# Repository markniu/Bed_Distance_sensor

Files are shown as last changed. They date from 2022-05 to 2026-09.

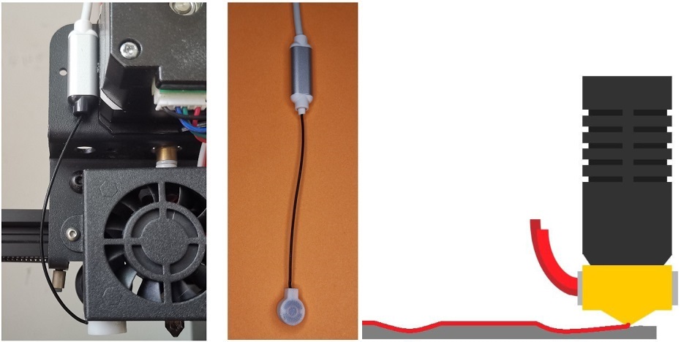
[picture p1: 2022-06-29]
doc/516115054.jpg

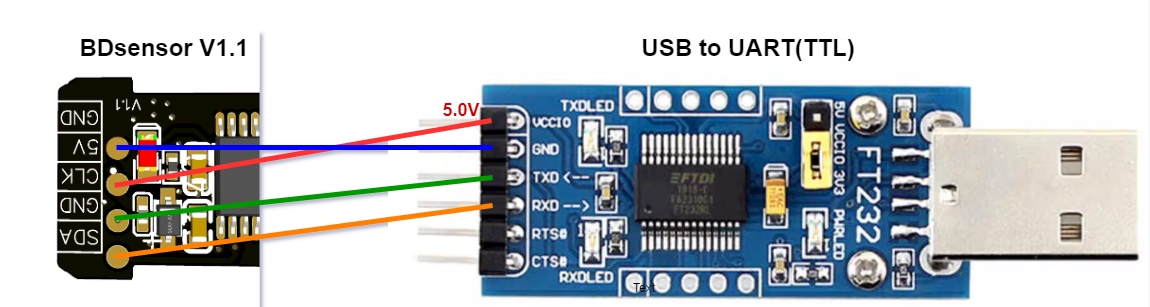
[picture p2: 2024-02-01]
doc/images/flashC51.jpg

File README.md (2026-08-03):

##  The Future of 3D printer Bed Leveling

[BDsensor](https://www.pandapi3d.com/bdsensor) is the first eddy bed level sensor that can work with 3D printer since 2022 and do fast bed leveling and adjust z axis in real time.
it can measure the bed distance at any point in real time without moving the z axis up and down.

Faster leveling, realtime compensation, high accuracy.

### Hardware:
* Shielded Coil
* Work with any GPIO pins(softI2C)
* The lightest and samllest eddy probe, 1.5g:
* Support high temperature chamber(120C) with the long cable probe [BDsensorM](https://github.com/markniu/Bed_Distance_sensor/wiki/BDsensor-M).
### Hardware Version
 . | hardware | firmware/software
--- | --- |---  
2022.6 | BDsensor VA, V1.0 | V1.0  
2023.4 | BDsensor VB, V1.1, the connector was changed | V1.1, support self reboot
2023.11 | BDsensor VB, V1.3, Upgrade the MCU to STM32 | V1.2, for stm32
2024.2  |              |V1.2c, [Support nozzle collision sensing](https://github.com/markniu/Bed_Distance_sensor/wiki/Collision-sensing)
2024.3  | BDsensorM V1.0             | V1.2c
2024.7  | BDsensorM V1.1             |  V1.2c, [Pins order](https://github.com/markniu/Bed_Distance_sensor/issues/178#issuecomment-2319621934) are changed in EXP1 connector
2025.1  |             | [Auto calibration](https://www.pandapi3d.com/post/new-feature-for-bdsensor)

### Software
 . | Marlin | Klipper
--- | --- |---  
Real Time leveling |:heavy_check_mark:| :heavy_check_mark:  
Fast bed mesh |:heavy_check_mark:| :heavy_check_mark: 
Fast bed mesh(No toolhead stop)|:heavy_check_mark: | :heavy_check_mark: 
Distance display |:heavy_check_mark: | :heavy_check_mark: 
Can bus toolhead|No | :heavy_check_mark: 
standby mode automatic while printing|:heavy_check_mark: | :heavy_check_mark: 
[KAMP](https://github.com/kyleisah/Klipper-Adaptive-Meshing-Purging) Adaptive Meshing & Purging |No | :heavy_check_mark: 
nozzle collision sensing|[Detail](https://github.com/markniu/Bed_Distance_sensor/wiki/Collision-sensing-for-Marlin):heavy_check_mark:  | :heavy_check_mark: 

### Benefit of Collision sensing
1.  **Auto z offset calibration**.
2.  **Overcome the temperature drift**.
     The temperature drift will only change the z_offset, it will rise or low the whole bed mesh, but does not change the bed mesh with this BDsensor. that means the bed mesh is the same even with [different temperature](https://www.pandapi3d.com/post/nozzle-collision-sensing-with-bdsensor).
3. Repeatability: **+/-0.005mm**
4. No external hardware and easy to adjust

### What is the difference between VB and VM?
The VB and VM (BDsensorM) share the same electronic design and firmware, so their functions and performance are essentially the same.
* VB: The coil and electronics are installed on the toolhead.
* VM: Only the lightweight 1.5 g coil is installed on the toolhead, while the PCB is mounted away from it, making the VM more suitable for high-temperature chambers up to [120C](https://github.com/markniu/Bed_Distance_sensor/wiki/BDsensor-M).

### Document  : [WiKi](https://github.com/markniu/Bed_Distance_sensor/wiki)

[History](https://hackaday.io/project/185096-0006mm-distance-resolution-sensor-for-3d-printer)

#### Mount STL:  [BLtouch_Compatible](https://www.thingiverse.com/thing:6098131) | [VzBoT](https://discord.com/channels/829828765512106054/1163237892957671424) | [Stealthburner Voron](https://www.printables.com/model/831679-lazy-bd-sensor-adapter-for-stealthburner-voron)

| Channel | Link |
|---|---|
| Discord | [discord.gg/z6ahddnGVU](https://discord.gg/z6ahddnGVU) |
| Facebook group | [facebook.com/groups/380795976169477](https://facebook.com/groups/380795976169477) |
| Where to buy | 🇺🇸 [fabreeko.com](https://fabreeko.com) <br>  🌏 [pandapi3d.com](https://pandapi3d.com) <br> 🇨🇳 [淘宝](https://shop62248922.taobao.com/)  <br> 🇩🇰 [3do.dk](https://3do.dk/12-abl-probe) |

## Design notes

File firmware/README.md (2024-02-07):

How to download the firmware into bdsensor:

[V1.3 STM32](https://github.com/markniu/Bed_Distance_sensor/wiki/Flash-BDsensor(stm32)-firmware)

[V1.1_STC](https://github.com/markniu/Bed_Distance_sensor/wiki/Flash-BDsensor(V1.1)-firmware)

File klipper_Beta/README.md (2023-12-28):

### This is the Beta version patch code for klipper.

if you like to test with this new code please run
```
cd  ~/Bed_Distance_sensor/klipper_Beta/
./install_BDsensor.sh
```
instead of 
```
cd  ~/Bed_Distance_sensor/klipper/
./install_BDsensor.sh
```

in the installation step of Klipper

https://github.com/markniu/Bed_Distance_sensor/wiki/Installing-for-Klipper

#### update: 
#### Add real time leveling. 
November 21, 2023

How to run?   

1. update the files in ~/Bed_Distance_sensor/klipper_Beta
2. go into the folder `cd ~/Bed_Distance_sensor/klipper_Beta`  and run` ./install_BDsensor.sh`
3. compile and flash the klipper.bin firmware again

4. Edit the start gcode in your slicer:
remove the auto bed leveling command `BED_MESH_CALIBRATE` and add `BDSENSOR_SET REAL_TIME_HEIGHT=`xx under the G28,
also z_tilt or gantry level is recommended. 
xx is the max z axis height that will do real time leveling automatically, here we just let this value the same as the first layer height in slicer setting.for example 0.3mm
```
G28
QUAD_GANTRY_LEVEL
G28
BDSENSOR_SET REAL_TIME_HEIGHT=0.3
```

note: this real time leveling works only with the BDsensor and Z motors are connected in the same MCU. 

And install the sensor coil as close to the nozzle as possible.

if you find the nozzle is too close or too far away the bed while printing, please do the calibration again.

#### update:
November 15, 2023

1, add new command:
```
BDSENSOR_VERSION                   //equals M102 S-1
BDSENSOR_CALIBRATE                //equals M102 S-6 
BDSENSOR_READ_CALIBRATION         //equals M102 S-5 
BDSENSOR_DISTANCE                 //equals M102 S-2 
BDSENSOR_SET                           // set value, now only for setting z_adjust, for example BDSENSOR_SET z_adjust=0.1

```
2, invert z_adjust direction as z_offset

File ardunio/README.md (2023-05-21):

Arduino testing code

This is a simple arduino testing code. It read the distance data from BDsensor after initial the communication port.

If you want to do more code by yourself for other application here is the protocol of data 

https://github.com/markniu/Bed_Distance_sensor/wiki/Data-Protocol

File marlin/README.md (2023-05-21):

Install marlin

https://github.com/markniu/Bed_Distance_sensor/wiki/Installing-Bed-Distance-Sensor

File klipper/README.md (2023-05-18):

Installing for Klipper

https://github.com/markniu/Bed_Distance_sensor/wiki/Installing-for-Klipper

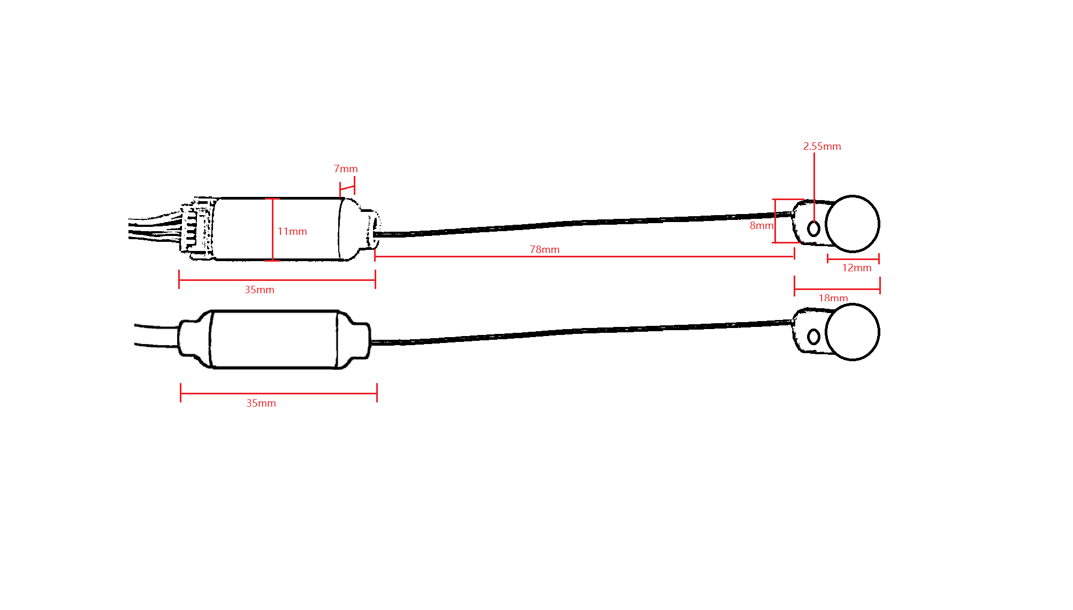
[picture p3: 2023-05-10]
hardware/size.png

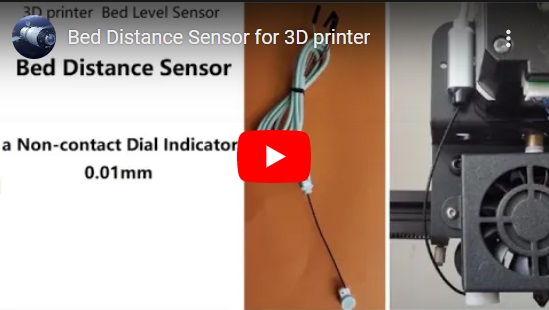
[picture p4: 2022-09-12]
doc/images/mainv.jpg

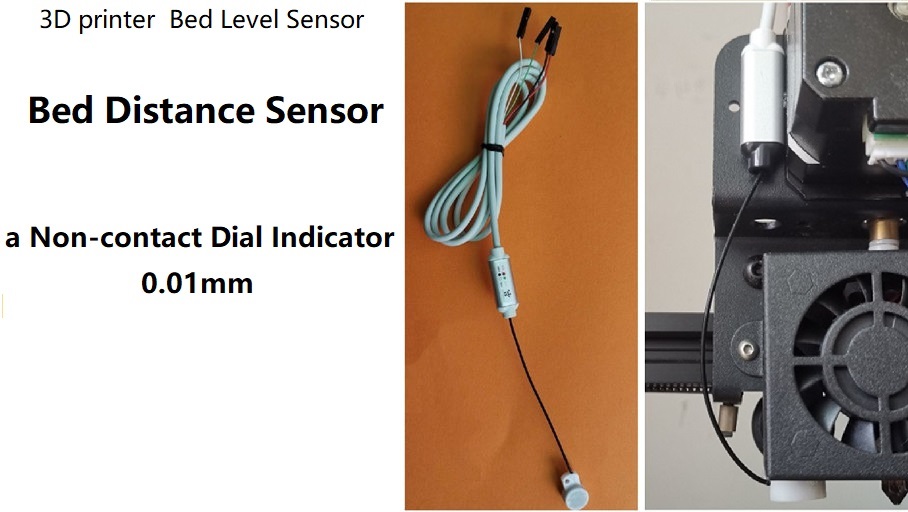
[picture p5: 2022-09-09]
doc/images/mainp2.jpg

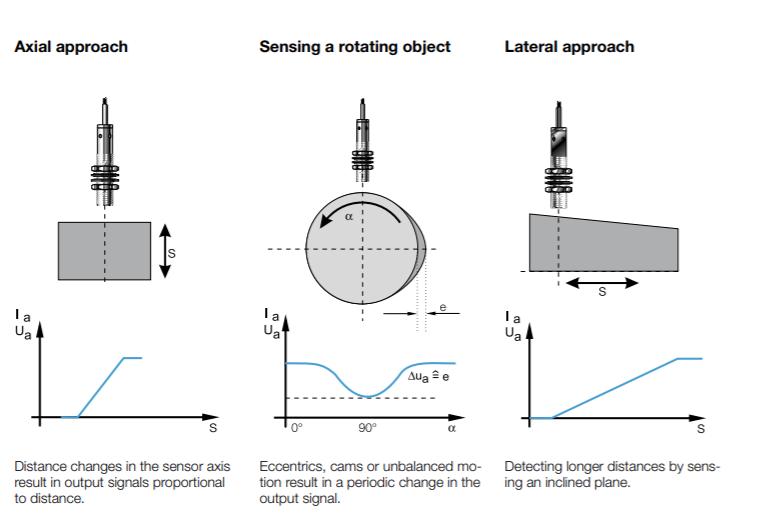
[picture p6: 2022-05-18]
doc/images/Shawn_1.png

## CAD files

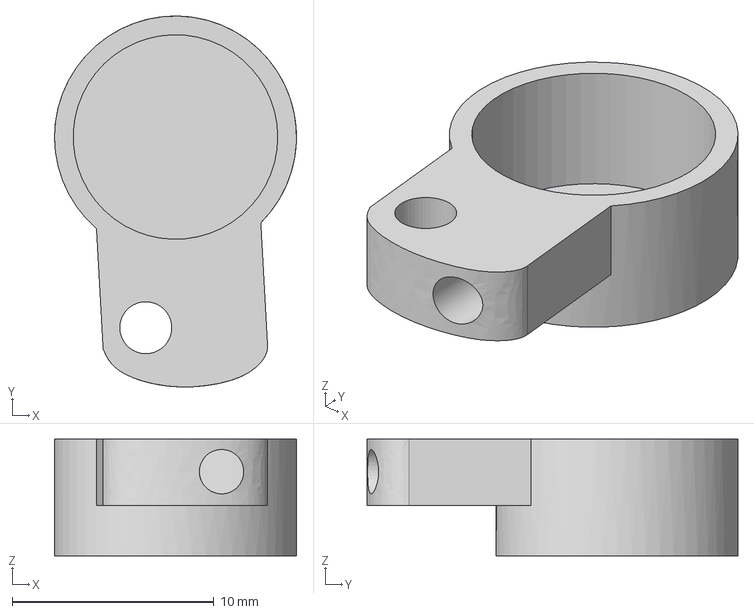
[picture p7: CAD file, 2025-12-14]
hardware/coil_case2025.step
12.0 x 18.4 x 5.80 mm

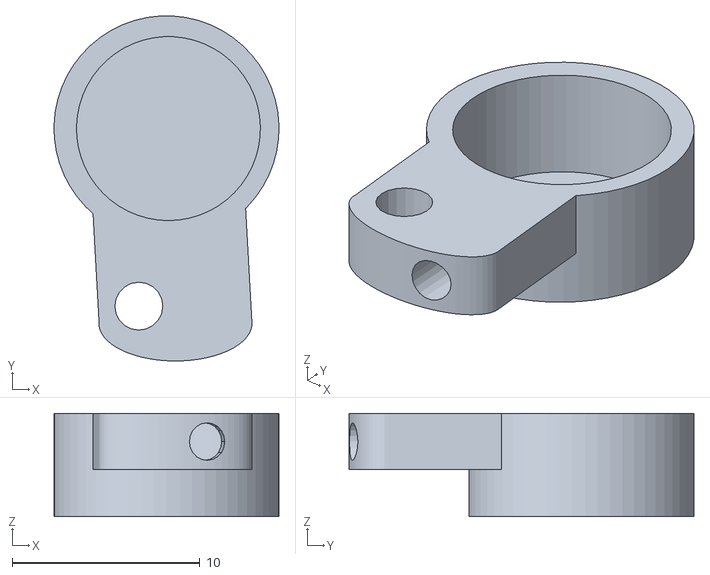
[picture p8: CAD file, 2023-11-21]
stl_size/coil_case_withoutcoil.stl
12.0 x 18.4 x 5.50

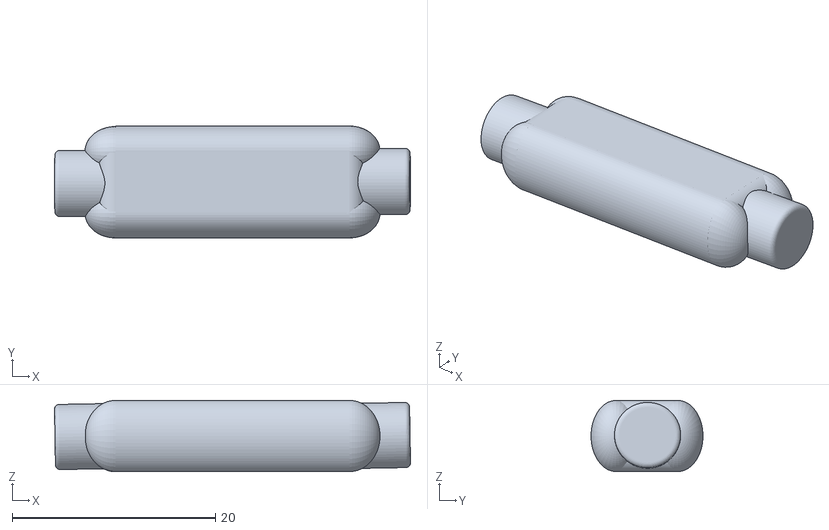
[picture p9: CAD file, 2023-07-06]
hardware/PCB_case.stl
35.0 x 11.0 x 7.00

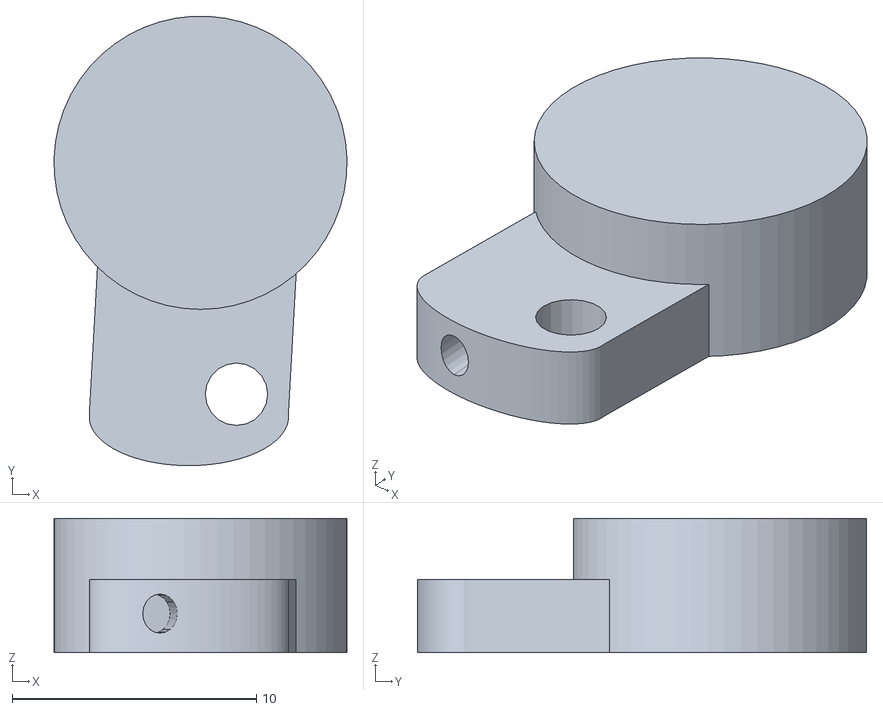
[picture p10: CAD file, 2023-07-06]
stl_size/Coil_casel.stl
12.0 x 18.4 x 5.50

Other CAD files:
hardware/coil_case2025.stl

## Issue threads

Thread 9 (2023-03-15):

Klipper reports: SHUTDOWN  Internal error on command:"M102"

neshami, 2023-03-15:

neshami, 2023-03-15:
Opened by error.
Sorry.

Closed 2023-03-15.

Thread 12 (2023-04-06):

Unable to calibrate sensor on SKR 2B

kendrickxy, 2023-04-06:
Hi,

I have an Anycubic Predator with SKR2B on Marlin.
I am using your branch of [Marlin](https://github.com/markniu/Marlin_for_pull), downloaded yesterday.

I followed the installation steps, but I'm not able to get it to calibrate.

At first, I tried swapping SDA and SCL, but without success.

I've made a few modifications in bdl.cpp from line 175:

```
if (config_state == -6) {
        //BD_I2C_SENSOR.BD_i2c_write(1019); // begin calibrate
        //delay(1000);
        SERIAL_ECHOLNPGM("ENABLE STEPPERS PREcalibrate");
        gcode.stepper_inactive_time = SEC_TO_MS(60 * 5);
        gcode.process_subcommands_now(F("M17 Z"));
        gcode.process_subcommands_now(F("G1 Z-0.05"));
        safe_delay(1000);
        SERIAL_ECHOLNPGM("SET POSITION PREcalibrate");
        gcode.process_subcommands_now(F("G92 Z0"));
        gcode.process_subcommands_now(F("G1 Z0.05"));
        gcode.process_subcommands_now(F("G92 Z0"));
        safe_delay(1000);
        SERIAL_ECHOLNPGM("WHILE START PREcalibrate")

        while (planner.get_axis_position_mm(Z_AXIS) > 0.15) {    // changed >0.00001 to >0.015 and >0.15
  
          safe_delay(10);   // changed (1) to (10)
        }
        SERIAL_ECHOLNPGM("WHILE END PREcalibrate");

        z_pose = 0.00001;
        safe_delay(100);
        BD_I2C_SENSOR.BD_i2c_write(CMD_START_CALIBRATE); // Begin calibrate
        SERIAL_ECHOLNPGM("Begin calibrate");
        safe_delay(200);
        config_state = -7;
      }
```

Below are the outputs for M102 S-1, S-5 and S-6.

```
// M102 S-1

ok
BDsensor version:???????????????????

// M102 S-5

ok
Calibrate data:0,1023, check:0
Calibrate data:1,1023, check:0
Calibrate data:2,1023, check:0
Calibrate data:3,1023, check:0
Calibrate data:4,1023, check:0
Calibrate data:5,1023, check:0
Calibrate data:6,1023, check:0
Calibrate data:7,1023, check:0
Calibrate data:8,1023, check:0
Calibrate data:9,1023, check:0
Calibrate data:10,1023, check:0
Calibrate data:11,1023, check:0
Calibrate data:12,1023, check:0
Calibrate data:13,1023, check:0
Calibrate data:14,1023, check:0
Calibrate data:15,1023, check:0
Calibrate data:16,1023, check:0
Calibrate data:17,1023, check:0
Calibrate data:18,1023, check:0
Calibrate data:19,1023, check:0
Calibrate data:20,1023, check:0
Calibrate data:21,1023, check:0
Calibrate data:22,1023, check:0
Calibrate data:23,1023, check:0
Calibrate data:24,1023, check:0
Calibrate data:25,1023, check:0
Calibrate data:26,1023, check:0
Calibrate data:27,1023, check:0
Calibrate data:28,1023, check:0
Calibrate data:29,1023, check:0
Calibrate data:30,1023, check:0
Calibrate data:31,1023, check:0
Calibrate data:32,1023, check:0
Calibrate data:33,1023, check:0
Calibrate data:34,1023, check:0
Calibrate data:35,1023, check:0
Calibrate data:36,1023, check:0
Calibrate data:37,1023, check:0
Calibrate data:38,1023, check:0
Calibrate data:39,1023, check:0

// M102 S-6

ok
ENABLE STEPPERS PREcalibrate
SET POSITION PREcalibrate
X:0.00 Y:0.00 Z:0.00 E:0.00 Count A:64374B:64374C:64374
X:0.00 Y:0.00 Z:0.00 E:0.00 Count A:64366B:64366C:64366
WHILE START PREcalibrate //stuck in an infinite loop
```

From what we can see in the log above, it's stuck in an infinite loop once reaching `while (planner.get_axis_position_mm(Z_AXIS)>0.00001)`

I've changed `>0.00001` to `>0.015`, but nothing changed.

Any tips on solving the issue?

Thanks

markniu, 2023-04-07:
seems that there had connect problem:
the `check:0 ` means the data check is wrong, the correct value should be `check:1`,
the message after M102 S-1 should be `BDsensor version:V1.0 pandapi3d.com`

did the z motor move while doing calibration?

markniu, 2023-04-07:
Just find the SKR 2 board use the stm32f4x that has higher processing speed than stm32f1, so you can try to increase the delay value from 20 to 100
`#define  I2C_BD_DELAY  100`

kendrickxy, 2023-04-07:
We're getting somewhere!

```
// M102 S-1

ok
BDsensor version:V1.0 pandapi3d.com

// M102 S-5

ok
Calibrate data:0,313, check:1
Calibrate data:1,327, check:1
Calibrate data:2,355, check:1
Calibrate data:3,406, check:1
Calibrate data:4,436, check:1
Calibrate data:5,451, check:1
Calibrate data:6,493, check:1
Calibrate data:7,493, check:1
Calibrate data:8,493, check:1
Calibrate data:9,566, check:1
Calibrate data:10,609, check:1
Calibrate data:11,632, check:1
Calibrate data:12,654, check:1
Calibrate data:13,663, check:1
Calibrate data:14,689, check:1
Calibrate data:15,711, check:1
Calibrate data:16,720, check:1
Calibrate data:17,743, check:1
Calibrate data:18,753, check:1
Calibrate data:19,764, check:1
Calibrate data:20,785, check:1
Calibrate data:21,794, check:1
Calibrate data:22,803, check:1
Calibrate data:23,820, check:1
Calibrate data:24,829, check:1
Calibrate data:25,838, check:1
Calibrate data:26,846, check:1
Calibrate data:27,854, check:1
Calibrate data:28,860, check:1
Calibrate data:29,867, check:1
Calibrate data:30,874, check:1
Calibrate data:31,880, check:1
Calibrate data:32,881, check:1
Calibrate data:33,887, check:1
Calibrate data:34,893, check:1
Calibrate data:35,897, check:1
Calibrate data:36,902, check:1
Calibrate data:37,907, check:1
Calibrate data:38,911, check:1
Calibrate data:39,911, check:1

// M102 S-6

ok
X:0.00 Y:0.00 Z:0.00 E:0.00 Count A:64375B:64375C:64375
X:0.00 Y:0.00 Z:0.00 E:0.00 Count A:64372B:64372C:64372
WHILE BEGIN
```

But as you see it's still stuck in the loop.

I home all 3 axis, send the command `M102 S-6` and the print head lower to the center of the plate as usual.
Once it's there, it's not able to come out of the loop though.

I'll try to run more tests.

markniu, 2023-04-08:
Hi, I think I know what's the problem is the home axis is not allowed before calibration. for the BDsensor is also used as the end stop of Z axis.

kendrickxy, 2023-04-09:
Hi,

At first, I tried to not home before (just tried again now), but it just runs the print head into the bed. not sure why.

Here are the logs I collected (with homing):

```
// M102 S-1

ok
BDsensor version:V1.0 pandapi3d.com

// M102 S-5

ok
Calibrate data:0,313, check:1
Calibrate data:1,327, check:1
Calibrate data:2,355, check:1
Calibrate data:3,406, check:1
Calibrate data:4,436, check:1
Calibrate data:5,451, check:1
Calibrate data:6,493, check:1
Calibrate data:7,493, check:1
Calibrate data:8,493, check:1
Calibrate data:9,566, check:1
Calibrate data:10,609, check:1
Calibrate data:11,632, check:1
Calibrate data:12,654, check:1
Calibrate data:13,663, check:1
Calibrate data:14,689, check:1
Calibrate data:15,711, check:1
Calibrate data:16,720, check:1
Calibrate data:17,743, check:1
Calibrate data:18,753, check:1
Calibrate data:19,764, check:1
Calibrate data:20,785, check:1
Calibrate data:21,794, check:1
Calibrate data:22,803, check:1
Calibrate data:23,820, check:1
Calibrate data:24,829, check:1
Calibrate data:25,838, check:1
Calibrate data:26,846, check:1
Calibrate data:27,854, check:1
Calibrate data:28,860, check:1
Calibrate data:29,867, check:1
Calibrate data:30,874, check:1
Calibrate data:31,880, check:1
Calibrate data:32,881, check:1
Calibrate data:33,887, check:1
Calibrate data:34,893, check:1
Calibrate data:35,897, check:1
Calibrate data:36,902, check:1
Calibrate data:37,907, check:1
Calibrate data:38,911, check:1
Calibrate data:39,911, check:1

// M102 S-6

ok
X:0.00 Y:0.00 Z:0.00 E:0.00 Count A:64354B:64354C:64354
X:0.00 Y:0.00 Z:0.00 E:0.00 Count A:64351B:64351C:64351
WHILE BEGIN
760.437
741.838
723.237
704.638
686.025
667.425
648.825
630.225
611.625
593.025
574.425
555.825
537.225
518.625
500.013
481.413
462.812
444.212
425.613
407.013
388.413
376.975
376.975
376.975
376.975
376.975
376.975
```
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
markniu, 2023-04-10:
Hi, could you share your config files and pins?  actually, I have not tested on the delta printer, the config for the endstop should be different as other printers.   and one other thing you should know is the homing process use the virtual Z_MIN_PIN
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

kendrickxy, 2023-04-10:
Hi,

Most of the issue is solved now :)
Here's the output:

```
// M102 S-1

ok
BDsensor version:V1.0 pandapi3d.com

// M102 S-5

ok
Calibrate data:0,44, check:1 Calibrate data:1,45, check:1
Calibrate data:2,47, check:1 Calibrate data:3,57, check:1
Calibrate data:4,57, check:1 Calibrate data:5,76, check:1
Calibrate data:6,95, check:1 Calibrate data:7,115, check:1
Calibrate data:8,139, check:1 Calibrate data:9,157, check:1
Calibrate data:10,185, check:1 Calibrate data:11,208, check:1
Calibrate data:12,224, check:1 Calibrate data:13,249, check:1
Calibrate data:14,273, check:1 Calibrate data:15,296, check:1
Calibrate data:16,325, check:1 Calibrate data:17,342, check:1
Calibrate data:18,367, check:1 Calibrate data:19,390, check:1
Calibrate data:20,411, check:1 Calibrate data:21,433, check:1
Calibrate data:22,456, check:1 Calibrate data:23,475, check:1
Calibrate data:24,494, check:1 Calibrate data:25,519, check:1
Calibrate data:26,535, check:1 Calibrate data:27,553, check:1
Calibrate data:28,570, check:1 Calibrate data:29,588, check:1
Calibrate data:30,605, check:1 Calibrate data:31,620, check:1
Calibrate data:32,637, check:1 Calibrate data:33,654, check:1
Calibrate data:34,672, check:1 Calibrate data:35,685, check:1
Calibrate data:36,695, check:1 Calibrate data:37,709, check:1
Calibrate data:38,723, check:1 Calibrate data:39,735, check:1

// M102 S-6

ok
X:0.00 Y:0.00 Z:0.00 E:0.00 Count A:30150B:30150C:30150
X:0.00 Y:0.00 Z:0.00 E:0.00 Count A:30150B:30150C:30150
WHILE START
WHILE END!
Begin calibrate
G1 Z0.0 ,Z:0.00 w:0,Zpose:0.00
G1 Z0.1 ,Z:0.10 w:1,Zpose:0.10
G1 Z0.2 ,Z:0.20 w:2,Zpose:0.20
G1 Z0.3 ,Z:0.30 w:3,Zpose:0.30
G1 Z0.4 ,Z:0.40 w:4,Zpose:0.40
G1 Z0.5 ,Z:0.50 w:5,Zpose:0.50
G1 Z0.6 ,Z:0.60 w:6,Zpose:0.60
G1 Z0.7 ,Z:0.70 w:7,Zpose:0.70
G1 Z0.8 ,Z:0.80 w:8,Zpose:0.80
G1 Z0.9 ,Z:0.90 w:9,Zpose:0.90
G1 Z1.0 ,Z:1.00 w:10,Zpose:1.00
G1 Z1.1 ,Z:1.10 w:11,Zpose:1.10
G1 Z1.2 ,Z:1.20 w:12,Zpose:1.20
G1 Z1.3 ,Z:1.30 w:13,Zpose:1.30
G1 Z1.4 ,Z:1.40 w:14,Zpose:1.40
G1 Z1.5 ,Z:1.50 w:15,Zpose:1.50
G1 Z1.6 ,Z:1.60 w:16,Zpose:1.60
G1 Z1.7 ,Z:1.70 w:17,Zpose:1.70
G1 Z1.8 ,Z:1.80 w:18,Zpose:1.80
G1 Z1.9 ,Z:1.90 w:19,Zpose:1.90
G1 Z2.0 ,Z:2.00 w:20,Zpose:2.00
G1 Z2.1 ,Z:2.10 w:21,Zpose:2.10
G1 Z2.2 ,Z:2.20 w:22,Zpose:2.20
G1 Z2.3 ,Z:2.30 w:23,Zpose:2.30
G1 Z2.4 ,Z:2.40 w:24,Zpose:2.40
G1 Z2.5 ,Z:2.50 w:25,Zpose:2.50
G1 Z2.6 ,Z:2.60 w:26,Zpose:2.60
G1 Z2.7 ,Z:2.70 w:27,Zpose:2.70
G1 Z2.8 ,Z:2.80 w:28,Zpose:2.80
G1 Z2.9 ,Z:2.90 w:29,Zpose:2.90
G1 Z3.0 ,Z:3.00 w:30,Zpose:3.00
G1 Z3.1 ,Z:3.10 w:31,Zpose:3.10
G1 Z3.2 ,Z:3.20 w:32,Zpose:3.20
G1 Z3.3 ,Z:3.30 w:33,Zpose:3.30
G1 Z3.4 ,Z:3.40 w:34,Zpose:3.40
G1 Z3.5 ,Z:3.50 w:35,Zpose:3.50
G1 Z3.6 ,Z:3.60 w:36,Zpose:3.60
G1 Z3.7 ,Z:3.70 w:37,Zpose:3.70
G1 Z3.8 ,Z:3.80 w:38,Zpose:3.80
G1 Z3.9 ,Z:3.90 w:39,Zpose:3.90
End calibrate data
```

The problem came from bdl.cpp as suspected. I simply replaced all `planner.get_axis_position_mm(Z_AXIS)` with `current_position.z`. Not sure why the command was off.

Still, I'm having some issues leveling the bed using automatic leveling `#define AUTO_BED_LEVELING_UBL`.

Here's my Z_MIN_PIN configuration:

```
#define Z_MIN_PIN          			         I2C_BD_SDA_PIN
#define Z_MIN_PROBE_PIN                  I2C_BD_SDA_PIN  //for skr2B
```

The command M119 outputs TRIGGERED when the nose is touching the bed. Though, not as the light turns on. I'm assuming it's working as expected.

Attached you can find my config files and pins.
[Configuration_adv.h.txt](https://github.com/markniu/Bed_Distance_sensor/files/11192941/Configuration_adv.h.txt)
[Configuration.h.txt](https://github.com/markniu/Bed_Distance_sensor/files/11192943/Configuration.h.txt)
[pins_BTT_SKR_V2_0_common.h.txt](https://github.com/markniu/Bed_Distance_sensor/files/11192946/pins_BTT_SKR_V2_0_common.h.txt)

markniu, 2023-04-24:
this issue of calibration is the same as https://github.com/markniu/Bed_Distance_sensor/issues/13#issuecomment-1517310271  , I have pulled it to marlin github, I think the next version of marlin will be updated.

Closed 2023-04-25.

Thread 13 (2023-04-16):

check:0

gacek4000, 2023-04-16:
Hi, I have SKR 1.4 and Marlin-2.1.2. After connecting the BD sensor I keep getting "Calibrate data:28,1023, check:0". The red LED lights up when something metal is under the sensor, then the "BD sensor Z" value on the display changes from 10.14 to 0.0
Any ideas ?

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

i set:

#define  I2C_BD_SDA_PIN    P0_01  // Please change to the actual number which the SDA wire is connected to your mainboard
#define  I2C_BD_SCL_PIN    P0_00  // Please change to the actual number which the SCL wire is connected to your mainboard
#define  I2C_BD_DELAY  20

//#define Z_MIN_PROBE_USES_Z_MIN_ENDSTOP_PIN
// Force the use of the probe for Z-axis homing
//#define USE_PROBE_FOR_Z_HOMING

#define BD_SENSOR
#define Z_SAFE_HOMING
and so on...

markniu, 2023-04-17:
you can replace those 2 files with the following link:
https://github.com/markniu/Marlin_for_pull/blob/bugfix-2.1.x/Marlin/src/feature/bedlevel/bdl/bdl.cpp
https://github.com/markniu/Marlin_for_pull/blob/bugfix-2.1.x/Marlin/src/gcode/probe/M102.cpp

then you can send M102 S-1 to read the version of BDsensor that can help you to check if the connection is success.

gacek4000, 2023-04-17:
before replacing the 2 files you described:
https://photos.app.goo.gl/fSZpwm4N7xALxyRs5

after change:
https://photos.app.goo.gl/6uFVhADqvVGMHKbYA
additionally, in this case, instead of "BD sensor Z: 10.14" on the screen, there is "Settings stored" from the beginning

i2c configuration didn't change anything in either case

markniu, 2023-04-18:
That should be all the old calibrate data in the BDsensor has been erased to default 0xFF,  Please sending M102 S-6 and waiting it finished.

gacek4000, 2023-04-18:
<facepalm>
ill check after job, thanks man !

gacek4000, 2023-04-18:
No, it doesn't work. It behaves the same as at the beginning: it starts moving down at the default speed. When I start the calibration, I have a screwdriver under the sensor, the LED was on red.

markniu, 2023-04-18:
the z axis should moving up.
and please make sure the calibration is finished by waiting there is message "End calibrate data" return back. or else there will return back 1023 and check 0 after M102 S-5

gacek4000, 2023-04-18:
when i send M102 S-6 the head goes down quite fast, nothing shows up in the console. homing and other head control from pronterface works fine

gacek4000, 2023-04-18:
I just replaced 'current_position.z' like kendrickxy and after 'M102 S-6' the head went down again, but in the console I had:

Begin calibration
G1Z0.0 ,Z:0.00
w:0,Zpose:0.00
G1Z0.1 ,Z:0.10
w:1,Zpose:0.10
G1Z0.2 ,Z:0.20
w:2,Zpose:0.20
G1Z0.3 ,Z:0.30
w:3,Zpose:0.30
G1Z0.4 ,Z:0.40
w:4,Zpose:0.40
G1Z0.5 ,Z:0.50

when I set
#define Z_MIN_PIN I2C_BD_SDA_PIN
#define Z_MIN_PROBE_PIN I2C_BD_SDA_PIN

printer behavior as above

[Configuration_adv.txt](https://github.com/markniu/Bed_Distance_sensor/files/11263324/Configuration_adv.txt)
[Configuration.txt](https://github.com/markniu/Bed_Distance_sensor/files/11263325/Configuration.txt)
[pins_BTT_SKR_common.txt](https://github.com/markniu/Bed_Distance_sensor/files/11263326/pins_BTT_SKR_common.txt)
[pins_BTT_SKR_V1_4.txt](https://github.com/markniu/Bed_Distance_sensor/files/11263327/pins_BTT_SKR_V1_4.txt)
[bdl.txt](https://github.com/markniu/Bed_Distance_sensor/files/11263328/bdl.txt)

gacek4000, 2023-04-18:
* M119 pokazuje 'z_probe: open' bez względu co jest pod czujnikiem (dioda świeci/ nie świeci)
* Z_MIN_PROBE_ENDSTOP_INVERTING true/false odpowiednio zmienia 'z_probe: open/triggered' ale głowa w obu przypadkach idzie na dół przy M102 S-6

markniu, 2023-04-19:
please add this `||P == Z_MIN_PROBE_PIN` in the endstop.cpp  like
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

and try M119 again

markniu, 2023-04-19:
> * M119 shows 'z_probe: open' no matter what is under the sensor (LED on/off)
> * Z_MIN_PROBE_ENDSTOP_INVERTING true/false changes 'z_probe: open/triggered' accordingly but the head goes down on M102 S-6 in both cases

The homing position of your delta printer is the in the max position, but the calibration position is in the zero, so the head will go down to the zero after the calibration command M102 S-6.  recommend to checking the position before calibration by send gcode M114

gacek4000, 2023-04-19:
i did what you said and:

M119
Reporting endstop status
x_max: open
y_max: open
z_max: open
z_probe: open
filament: open
ok

with metal under sensor. calibration process - still the same.

'#define Z_MIN_PROBE_PIN                  P0_10'    is this correct ? When I uncomment it, the program doesn't compile

markniu, 2023-04-20:
although I haven't delta printer but have one SKRV1.4 board, I will run it on that board late or tomorrow late. and will update that after testing.

markniu, 2023-04-21:
[bdl.zip](https://github.com/markniu/Bed_Distance_sensor/files/11292705/bdl.zip)
I have test it with skrV1.4 board, and it can do calibration and M119 success.  please replace the those files. including the file probe.h in Marlin\src\module folder. and don't homing printer before calibration.

gacek4000, 2023-04-23:
It works ! everything works, screen and calibration. Thanks a lot buddy :) What have you done? Have I mixed something up?

markniu, 2023-04-24:
That's great, thanks for test it on delta printer.
the position value got by  `planner.get_axis_position_mm(Z_AXIS)` is not zero in zero position for delta printer, so I fixed it by  `planner.get_axis_position_mm(Z_AXIS)-pos_zero_offset`

gacek4000, 2023-04-25:
Hi again, I guess I rushed to announce success :( calibration works, M119 also but:
when trying to calibrate the delta (G33) or when trying to print a test print, the head goes down and does not react to the presence of the table under the sensor and collides with the table.
i set "#define DELTA_HEIGHT" and #define "Z_MAX_POS" to be less than the height of the printer. Then, when going down, even though I put metal under the sensor (the LED is on), the printer does not respond and then goes back up and I get a "Homing Failed" error
Any ideas ?

Closed 2023-04-24.

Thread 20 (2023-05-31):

Question: What is the operating temperature/ melting point?

billgeek, 2023-05-31:
As most that have built a Voron extruder will know, inductive probes tend to melt due to the constant exposure of the probe to the heated bed, especially when printing using ABS where the bed sits at around 85C.

What temperature resistance does this sensor have and will it deform or melt while in operation?

markniu, 2023-06-02:
the max operating temperature of all the components is above 80C including the wires.
the max work temperature of the inside coil is 120C, and 170C for the nylon case.

Closed 2023-06-02.

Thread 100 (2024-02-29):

Endstop triggered during retract when it is not triggered.

nullifyr, 2024-02-29:
Mark, I added another z axis motor to my SKR2 and put the gantry on ball screws to get rid of gantry sag that I could not tune away.
Calibration works great. Testing the measurement after calibration, the Z axis is very accurate now.
But now I can't get the Z to home. No matter where I place the gantry, well above the bed or very near it, I get a "Endstop z still triggered after retract" even if the M119 shows the endstop is open when I start homing.
Nothing changed on the printer other than the addition of a 2209 stepper driver
I attached the log with the relevant dump
[sklippy.log](https://github.com/markniu/Bed_Distance_sensor/files/14441199/sklippy.log)
[printerlog.txt](https://github.com/markniu/Bed_Distance_sensor/files/14441200/printerlog.txt)
You can see in the printer log where I calibrate, measure, move the gantry down above the trigger point, measure and check triggers then repeat that after moving the gantry below the trigger point.
I also have re-cloned the bdsensor repo, made a clean firmware and flashed it.
This is the newest version of your sensor with the long sensor lead that you sent along with my last order. It definitely worked before this change. I believe there is some bug I introduced.

nullifyr, 2024-02-29:
I turned on collision homing and it works now?
```
G28
BDsensorVer:V1.2c pandapi3d ,switch_mode=1,collision_homing=1
pos:0.80 new:0.87 auto adjust Z axis +0.07mm,Raw data from 748.0 to 755.0
```

markniu, 2024-02-29:
seems it was triggered in the place where the nozzle did not touch on the bed.
maybe the homing speed and second homing speed of z motor is too slow.

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

nullifyr, 2024-02-29:
I raised the homing to 8 and second homing to 0.8, but the nozzle is still ~3mm away from the bed when at Z0

markniu, 2024-02-29:
What's the configuration of the BDsensor , stepper_z  safe_z_home? and they are not in the log file.

> Mark, I added another z axis motor to my SKR2 and put the gantry on ball screws to get rid of gantry sag that I could not tune away. Calibration works great. Testing the measurement after calibration, the Z axis is very accurate now. But now I can't get the Z to home. No matter where I place the gantry, well above the bed or very near it, I get a "Endstop z still triggered after retract" even if the M119 shows the endstop is open when I start homing. Nothing changed on the printer other than the addition of a 2209 stepper driver I attached the log with the relevant dump [sklippy.log](https://github.com/markniu/Bed_Distance_sensor/files/14441199/sklippy.log) [printerlog.txt](https://github.com/markniu/Bed_Distance_sensor/files/14441200/printerlog.txt) You can see in the printer log where I calibrate, measure, move the gantry down above the trigger point, measure and check triggers then repeat that after moving the gantry below the trigger point. I also have re-cloned the bdsensor repo, made a clean firmware and flashed it. This is the newest version of your sensor with the long sensor lead that you sent along with my last order. It definitely worked before this change. I believe there is some bug I introduced.

markniu, 2024-02-29:
try to increase the second homing speed to 3
> I raised the homing to 8 and second homing to 0.8, but the nozzle is still ~3mm away from the bed when at Z0

nullifyr, 2024-02-29:
Second homing at 1.6 seems to have done the trick
[klippy.log](https://github.com/markniu/Bed_Distance_sensor/files/14441629/klippy.log)
Here is the full Klipper log.
If I turn off collision homing I am back to the retract error.

nullifyr, 2024-02-29:
Here is the log after I change back to no
[klippy.log](https://github.com/markniu/Bed_Distance_sensor/files/14441670/klippy.log)

markniu, 2024-02-29:
how about take the bdsensor off the hotend also the whole wires for bdsensor to avoid the noise from other wires , and put the sensor coil close or away from the bed while homing to see if it works as expected.

nullifyr, 2024-02-29:
OK I tried all your suggestions, it did not change the retract message with collision homing off.
The behavior never changes, close to the bed or far away.
I even put the coil on a 100mm standoff so it was far away from the toolhead. No change there.
I tried the older version of the sensor too. It does the same thing.

nullifyr, 2024-03-02:
Is there any way to get bdsensor to report the state of the endstops before it performs any movement?
I cannot figure out how to fix my problem here.

Collision homing does work, but it occasionally reads > 0.3mm of adjustment
is there any way to set a maximum adjustment the collision homing will allow before it fails?
for instance, if there is a glob of plastic on the nozzle and we do collision homing, the adjustment is wild
`pos:0.80 new:1.62 auto adjust Z axis +0.82mm,Raw data from 81.0 to 124.0`
Needless to say this print failed instantly because the nozzle was several layers higher than it should have started at.

markniu, 2024-03-02:
I also tryed your configure and did not met this problem, could you take a video about that homing process?
> OK I tried all your suggestions, it did not change the retract message with collision homing off. The behavior never changes, close to the bed or far away. I even put the coil on a 100mm standoff so it was far away from the toolhead. No change there. I tried the older version of the sensor too. It does the same thing.

nullifyr, 2024-03-02:
[https://youtu.be/gmcaOjzPdys](https://youtu.be/gmcaOjzPdys)

The gantry never tries to drop down. The Z is immediately triggered. But, you see me move over the trigger range (the move was 10mm) and I did M119, it was open before I pressed home.

Other things I have done
Corrected the Z motor phase and direction so both motors have the same configuration.
Trammed the bed again just to be sure

markniu, 2024-03-02:
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

you can replace the BDsensor.py with this new one that I add a debug info into the code,
[BDsensor.zip](https://github.com/markniu/Bed_Distance_sensor/files/14468116/BDsensor.zip)

nullifyr, 2024-03-02:
[klippy (12).log](https://github.com/markniu/Bed_Distance_sensor/files/14468290/klippy.12.log)`

Klipper state: Shutdown

triggered at 10.150 mm !

Endstop z still triggered after retract

home_start:0.800000

home_start:0.800000

BDsensorVer:V1.2c pandapi3d ,switch_mode=1,collision_homing=0

G28`

nullifyr, 2024-03-02:
I tried some more things but still no joy
-Removed TMC Autotuning and KAMP
-Tried different pins for SDA/SCL
-Went back to the old version of the sensor with a short lead for the coil

With the old version I can see the LED while the homing is in process. It never lights up like it does when it is actually triggered.
I am so confused by that.

nullifyr, 2024-03-04:
YES.
That fixed it.

```
11:04 AM
Z axis triggered at 0.040 mm,auto adjusted by BDsensor.
11:04 AM
home_start:0.100000
11:04 AM
home_start:0.100000
11:04 AM
BDsensorVer:V1.2c pandapi3d ,switch_mode=1,collision_homing=0
```

nullifyr, 2024-03-04:
Could you clarify what the problem actually was?

markniu, 2024-03-12:
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

Hello, just want to know if it is totally fixed the problem in your printer, and that never happened again? did you try other value of this position_endstop ?

nullifyr, 2024-03-12:
Totally fixed the problem.
Unless I raise the position_endstop to 0.8mm or more. Then the behavior comes back. This is fine for me as the coil is 0.625mm away from the nozzle tip, but I think it would be a problem for anyone who wanted to mount higher than 0.8mm.

markniu, 2024-03-13:
Thanks, that's also confused me for that I have not repeated this problem in myside. I will debug more. but now I think it could be the communication problem by the signal noise on the cable.

here the position_endstop is not the mount height. it just the trigger position that we set to avoid the nozzle crash into bed with higher homing speed.

markniu, 2024-03-22:
> Totally fixed the problem. Unless I raise the position_endstop to 0.8mm or more. Then the behavior comes back. This is fine for me as the coil is 0.625mm away from the nozzle tip, but I think it would be a problem for anyone who wanted to mount higher than 0.8mm.

someone feedbacked me that the latest update of BD_sensor.c had fixed this issue with  position_endstop : 0.8mm, maybe you can try it if you have time and feedback here too. thanks!

nullifyr, 2024-03-23:
```
Klipper state: Shutdown
triggered at 10.150 mm
Endstop z still triggered after retract
home_pos:80
home_pos:80
BDsensorVer:V1.2c pandapi3d ,switch_mode=1,collision_homing=0,collision_cal=0
G28
Klipper state: Disconnect
FIRMWARE_RESTART
Z triggered at 0.700 mm,auto adjusted.
home_pos:70
home_pos:70
BDsensorVer:V1.2c pandapi3d ,switch_mode=1,collision_homing=0,collision_cal=0
G28
```
No change in behavior. I agree it seems like noise, but when the configuration has position_endstop at 0.7mm the sensor works very well. Well enough that I can level the gantry to 0.008mm in 3 tries. Wouldn't noise affect the readings for probes like that?

Could you make a version that raises the Z to some set distance over the trigger height before it tries to home? I know Klipper already has this logic in the homing code, but I can't think of any other way to test this.

Closed 2024-03-04.

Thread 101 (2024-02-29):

Issue with ramps 1.4

luco85, 2024-02-29:
Hi, i tried to install to my printer with ramps 1.4, but klipper crash and shutdown whenr i send any commansd whit M102. I have a bltouch working and no issue when installed bd patch. There is any chance to use with this board or need to use the gpio pin of rpi? In this case can i use any gpio for SDA and CLK?

markniu, 2024-02-29:
you can use the gpio of rpi, #92

luco85, 2024-02-29:
Ok i'll try. Another issue that i had was after add the moonraker update section. After that i had  an UNKNOW state to update section of mainsail. Any info?

luco85, 2024-03-01:
> you can use the gpio of rpi, #92

It work fine with rpi. For UNKNOW label in update manager do you have any tip?

luco85, 2024-03-04:
I wanted to ask you to do the integration with klipper! good News!
I installed bd sensor to rpa and work fine! very nice device. thank you!

luco85, 2024-03-06:
@markniu hi! Yesterday i tried to use the collision feature. I update bdsensor section with homing and calibration collision set to 1. When i read sensor it respond firmware v1.2, switch mode 0, collision homing 1, collision calibrate 1. When i run calibration it work as before, it not homing but start to calibrate. I updated your code to last and flashed all mcu. I noticed when i run your code to update i have an error. So need to uninstall and reinstall to update

markniu, 2024-03-06:
The respond firmware should be `V1.2c` not `V1.2 ` , else maybe the firmware did not flash successfully.

luco85, 2024-03-06:
I suspected this so yesterday I ordered st link to flash device

luco85, 2024-03-09:
@markniu hi, there is a typo error here
Marco for display distance on Screen
not Marco but Macro ;)

markniu, 2024-03-10:
> @markniu hi, there is a typo error here Marco for display distance on Screen not Marco but Macro ;)

Thank you :)

markniu, 2024-03-28:
the latest BD_sensor.c code on github has fixed the issue on ramps1.4 board.

Closed 2024-03-28.

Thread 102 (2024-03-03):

Can't home with new firmware

Mharasim1, 2024-03-03:
After flashing new firmware im getting this error when trying to home z: Unable to read tmc uart 'stepper_z' register DRV_STATUS
Z axis moves fine if i use SET_KINEMATIC_POSITION
There are a few BD Sensor errors in klippy.log
[klippy (9).log](https://github.com/markniu/Bed_Distance_sensor/files/14473712/klippy.9.log)

markniu, 2024-03-04:
did it happen every time while homing? how about send M102 S-1 before homing gcode G28?

Mharasim1, 2024-03-04:
I get this after sending M102 S-1 : BDsensorVer:V1.1bpandapi3d.com ,switch_mode=1,collision_homing=1,collision_cal=1
but it still doesent home.
It was homing before i flashed new firmware to the sensor
@markniu

markniu, 2024-03-04:
the bd sensor and tmc are two independed from the hardware and code.
one way you can try to debug:  remove the BDsensor section and replace the `endstop_pin: probe:z_virtual_endstop` with `endstop_pin:PB8` in the stepper_z section, move the nozzle far enough from the bed and home again

markniu, 2024-03-04:
for the klippery source code, seems the error is that it can not read data from the tmc and timeout.
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

Mharasim1, 2024-03-05:
I removed bd sensor section and and removed endstop_pin: probe:z_virtual_endstop and it tried to home fine.
but when i add bd sensor to config i get tmc error

markniu, 2024-03-07:
could you try to replace a code in the BDsensor.py as following? that will let the homing process as old firmware.

before
```
  def home_start(self, print_time, sample_time, sample_count, rest_time,
                   triggered=True):
        self.BD_Sensor_Read(2)
        if "V1." not in self.bdversion:
            self.BD_version(self.gcode)
        clock = self.mcu_endstop.print_time_to_clock(print_time)
```

after

```

  def home_start(self, print_time, sample_time, sample_count, rest_time,
                   triggered=True):
        self.BD_Sensor_Read(2)
        self.switch_mode = 0
        clock = self.mcu_endstop.print_time_to_clock(print_time)

```

Closed 2024-04-15.

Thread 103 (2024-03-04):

Internal error on command:"G28" while homing Z axis

BUGBEAR7, 2024-03-04:
Hello ,

Recently installed on my Enderwire , after calibration Z axis is not homing gets Internal error on command:"G28"
Here is the [klippy.log](https://github.com/markniu/Bed_Distance_sensor/files/14481264/klippy.log)
I am not sure what I am doing wrong , Sensor is v1.2

markniu, 2024-03-04:
the reason is the aliases board pins, please use the PB8 PB9 instead of PROBE_2 PROBE_1

BUGBEAR7, 2024-03-04:
Thanks for that , it fixed the issue.

Closed 2024-03-04.

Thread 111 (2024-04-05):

No data or corrupt data from BDsensor( )

hidara2000, 2024-04-05:
Hi,
I have two of these devices and am getting the same error on both

## WIRING
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

## EBB sb2209 from guide
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

Servos = PB9
Probe = PB8

## Klipper Settings
```
[BDsensor]
# Don't use aliases for the board pins
sda_pin: EBBCan: PB9 # from https://github.com/markniu/Bed_Distance_sensor/issues/50
scl_pin: EBBCan: PB8
delay: 20 # 20us per pulse, this value should be >=18 but must be below 30
z_offset:0 #  within -0.6 to 0.6mm
x_offset: 0
y_offset: 25.0
no_stop_probe: # fast probe that the toolhead will not stop at the probe point,disable it by commenting out.
position_endstop: 0.5 #the Z axis will be triggered after it measured the distance is below this value(mm) while homing z, recommend value is 0.5~1.0
#speed:0.8 # this speed only works for the z tilt and PROBE_ACCURACY command.
collision_homing:0 #  set it 1 to enable homing with nozzle collision sensing.
collision_calibrate:0 # set it 1 to enable auto calibrate BDsensor with nozzle collision sensing.
```

## Flashing using canbus result
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

## BDsensor.py exists before compiling and flashing clean
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

## WHAT I'VE TRIED
- swap   PB8 for  PB9 in klipper settings
- check wires for shorts and continuity - all good

## Results from commands
```
M119
```
x:open y:open z:TRIGGERED # whether triggered or not
*NOTE: I can see the light triggering to detect metal when I bring a spanner close to the sensor*

```
M102 S-1
```
No data or corrupt data from BDsensor( ), Please check connection

```
BDSENSOR_VERSION
```
No data or corrupt data from BDsensor( ), Please check connection

```
BDSENSOR_READ_CALIBRATION
```
No data or corrupt data from BDsensor( ), Please check connection
BDSensor mounted too close! please mountthe BDsensor 0.2~0.4mm higher

hidara2000, 2024-04-05:
Also tried direct connection to MKS v1.3 board and same issue. Bl touch with confi changes works perfectly using the same pins

markniu, 2024-04-05:
Hello,
Seems you need to switch the SDA and CLK pin in the printer.cfg:
```
sda_pin: EBBCan: PB8
scl_pin: EBBCan: PB9
```

hidara2000, 2024-04-05:
Cheers for the reply. That's what I had originally but changed it as per the comment in this post https://github.com/markniu/Bed_Distance_sensor/issues/50

either way I've tried both

markniu, 2024-04-05:
you can change it back to the correct order and try again.
if still the same,  try to connect the bdsensor to the mainboard for finding out where the problem is.

hidara2000, 2024-04-05:
I've already tried that and connected directly to the SKR v1.3

markniu, 2024-04-05:
the endstop pin on the skr v1.3 for the bltouch doesn't work with bdsensor, you can use the pin in EXP1 or EXP2 for bdsensor.

> SKR v1.3

hidara2000, 2024-04-05:
I have the EBB SB2209 canbus and need to get it working with this. If it needs I2C I found (image below) in the schematics but cant figure out which pins these are.

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

markniu, 2024-04-05:
BDsensor use the i2c, but not standard i2c.
I have tested the other version of EBB board that can work with bdsensor with the BLtouch port.
do you check the wires with multimeter?

> Also just a quick one. The pins for the BDsensor mention sda and clk. Does it use I2c? if so, I wonder if the pins for BLTouch on the EBB SB2209 are compatible?

hidara2000, 2024-04-05:
do you check the wires with multimeter?

I checked for continuity and shorts

markniu, 2024-04-05:
ok, because I have met the connection loosen problem to the mainboard before.
are there any other unused pins on the board?you can try that, but don't use the endstop pins.

markniu, 2024-04-05:
also did the led work? the led on the bdsensor should be light on if it detects the metal.

hidara2000, 2024-04-05:
LED works as expected

markniu, 2024-04-05:
you can also try to increase the delay value in the [BDsensor] section from 20 to 40, that will slow down the data transfer speed.

Terrradives, 2024-04-06:
I also have been having the same symptoms and issues the last few days.  I'm plugged into a octopus 1.1.  pb6 &7 pins.  lights work.  triggered always active.  M102 codes return the same.

hidara2000, 2024-04-10:
Hi @Terrradives ,
Did you manage to get it working?

hidara2000, 2024-04-10:
@markniu

Any suggestions on how to connect directly to a Pi and if there is a Python script I can run to test the device?

markniu, 2024-04-10:
yes, you can test it with the gpio on the Pi,  connect the bdsensor to the gpio on the PI like gpio17 and gpio27.

[BDsensor]
....
scl_pin = host:gpio17
sda_pin = host:gpio27

compile and flash firmware:
https://www.klipper3d.org/RPi_microcontroller.html

https://github.com/markniu/Bed_Distance_sensor/issues/84

hidara2000, 2024-04-10:
Donno if this will help but I added the following lines to the BDsensor.py
``` python
attrs = vars(self)
attrs = ('\n'.join("%s: %s" % item for item in attrs.items()))

self.gcode.respond_info(f"{attrs}")
self.gcode.respond_info("No data or corrupt data from BDsensor(%s), "
                                    "Please check connection"%self.bdversion)
```
and the response was
```
printer: <__main__.Printer object at 0x7f7f9350d0>
config:
name: BDsensor
z_adjust: 0.0
z_offset: 0.0
position_endstop: 0.5
stow_on_each_sample: True
no_stop_probe:
collision_homing: 0
collision_calibrate: 0
activate_gcode:
deactivate_gcode:
collision_calibrating: 0
switch_mode: 1
bdversion:             
next_cmd_time: 0.0
action_end_time: 0.0
sda_pin_num: PB8
mcu:
_invert: 0
oid: 2
mcu_endstop:
_invert_endstop: 0
oid_endstop: 2
endstop_pin_num: PB8
endstop_bdsensor_offset: 0
cmd_queue:
trapq:
trapq_append:
trapq_finalize_moves:
stepper_kinematics:
bd_sensor:
gcode:
I2C_BD_receive_cmd2: None
gcode_move:
bedmesh: None
bd_value: 10.24
results: []
finish_home_complete: None
wait_trigger_complete: None
multi: OFF
adjust_range: 0
old_count: 1000
homeing: 0
reactor:
status_dis: None
_rest_ticks: 0
_trdispatch:
_trsyncs: [, ]
ncont: 0
z_last: 0
I2C_BD_receive_cmd:
_home_cmd:
toolhead:
```

markniu, 2024-04-10:
> Donno if this will help but I added the following lines to the BDsensor.py
>
that reported all the data is 10.24(`bd_value: 10.24`) , means no data returned from the sda pin.

hidara2000, 2024-04-10:
Interesing....
When I connected the device to the EBB canbus or directly to the SKR v1.3 I got errors

Now when connected directly to the pi I get
```
BDSENSOR_VERSION
```
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

markniu, 2024-04-10:
yes, that's weird.

markniu, 2024-04-10:
you can try to test it by connecting it to the pins on the EXP1 of SKR

Terrradives, 2024-04-10:
I have not yet.  I’m kind of hoping there are tests I can rule things out with.  I’ve switched pins I was using on the octopus board, so I don’t think it’s board or pins.  I’ve got a bltouch currently working on those pins.  It’s not wire.  So I’m left kind of thinking how do I verify I’ve got a correctly flashed boards or verify the sensor is fully functional.Sent from my iPhoneOn Apr 10, 2024, at 12:26 AM, hidara2000 ***@***.***> wrote:
Hi @Terrradives ,
Did you manage to get it working?

—Reply to this email directly, view it on GitHub, or unsubscribe.You are receiving this because you were mentioned.Message ID: ***@***.***>

hidara2000, 2024-04-13:
**GOT IT WORKING :)**

## What didn't work
1. Made 3 sets of cables from the supplied ribbon.
Used the proper crimping tool.
Checked for shorts and continuity.
None of these cables worked on the BDsensor but all worked for a BL-touch I had lying around
2. Reflashed firmware on EBB and SKR

## What DID work
1. Made a set of cables using some 26AWG silicone cables. 1st set worked on both BL touch and BDsensor

hidara2000, 2024-04-13:
PS for anyone else, here's a mount I made for the CW2 & Stealthburner. You don't need to modify any existing parts.

https://www.printables.com/model/831679-lazy-bd-sensor-adapter-for-stealthburner-voron

markniu, 2024-04-13:
> PS for anyone else, here's a mount I made for the CW2 & Stealthburner. You don't need to modify any existing parts.
>
> https://www.printables.com/model/831679-lazy-bd-sensor-adapter-for-stealthburner-voron

Thanks for share!

Terrradives, 2024-04-13:
Is there any chance you’d be willing to make a1.5 meter set and ship them to the USA?Sent from my iPhoneOn Apr 13, 2024, at 12:59 AM, hidara2000 ***@***.***> wrote:
GOT IT WORKING :)
What didn't work

Made 3 sets of cables from the supplied ribbon.
Used the proper crimping tool.
Checked for shorts and continuity.
None of these cables worked on the BDsensor but all worked for a BL-touch I had lying around
Reflashed firmware on EBB and SKR

What DID work

Made a set of cables using some 26AWG silicone cables. 1st set worked on both BL touch and BDsensor

—Reply to this email directly, view it on GitHub, or unsubscribe.You are receiving this because you were mentioned.Message ID: ***@***.***>

hidara2000, 2024-04-14:
@Terrradives
Honestly I would diy this. Just grab the following
- https://www.amazon.com/dp/B08RMQP6YP?ref=ppx_yo2ov_dt_b_product_details&th=1
- https://www.amazon.com/Electrical-26-Flexible-Silicone-different/dp/B07G2LRX68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

For each of the 5 wires, cut off the male ends of two pre-crimped wires and solder the length you need in between. The set comes with heat shrink as well :)

Closed 2024-04-14.

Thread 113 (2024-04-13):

re:Beta, after running 'install_BDsensor.sh', firmware compilation fails with Error 255

m3hrz4d, 2024-04-13:
I cloned the repo, then successfully ran 'klipper_Beta/install_BDsensor.sh', but when trying to compile firmware, it fails just before the end with Error 255" Any ideas that could point me in the right direction?
```
make
Using default symbol values (no '/home/sonic/klipper/.config')
Configuration saved to '/home/sonic/klipper/.config'
  Creating symbolic link out/board
Loaded configuration '/home/sonic/klipper/.config'
Configuration saved to '/home/sonic/klipper/.config'
  Creating symbolic link out/board
  Creating symbolic link out/board
  Building out/autoconf.h
  Compiling out/src/sched.o
  Compiling out/src/command.o
  Compiling out/src/basecmd.o
  Compiling out/src/debugcmds.o
  Compiling out/src/initial_pins.o
  Compiling out/src/gpiocmds.o
  Compiling out/src/stepper.o
  Compiling out/src/endstop.o
  Compiling out/src/trsync.o
  Compiling out/src/adccmds.o
  Compiling out/src/spicmds.o
  Compiling out/src/sdiocmds.o
  Compiling out/src/i2ccmds.o
  Compiling out/src/pwmcmds.o
  Compiling out/src/buttons.o
  Compiling out/src/tmcuart.o
  Compiling out/src/neopixel.o
  Compiling out/src/pulse_counter.o
  Compiling out/src/lcd_st7920.o
  Compiling out/src/lcd_hd44780.o
  Compiling out/src/spi_software.o
  Compiling out/src/i2c_software.o
  Compiling out/src/thermocouple.o
  Compiling out/src/sensor_adxl345.o
  Compiling out/src/sensor_angle.o
  Compiling out/src/sensor_mpu9250.o
  Compiling out/src/sensor_lis2dw.o
  Compiling out/src/sensor_ldc1612.o
  Compiling out/src/sensor_bulk.o
  Compiling out/src/BD_sensor.o
  Compiling out/src/stm32/watchdog.o
  Compiling out/src/stm32/gpio.o
  Compiling out/src/stm32/clockline.o
  Compiling out/src/stm32/dfu_reboot.o
  Compiling out/src/generic/crc16_ccitt.o
  Compiling out/src/generic/armcm_boot.o
  Compiling out/src/generic/armcm_irq.o
  Compiling out/src/generic/armcm_reset.o
  Compiling out/src/../lib/stm32f4/system_stm32f4xx.o
  Compiling out/src/stm32/stm32f4.o
  Compiling out/src/generic/armcm_timer.o
  Compiling out/src/stm32/gpioperiph.o
  Compiling out/src/stm32/adc.o
  Compiling out/src/stm32/i2c.o
  Compiling out/src/stm32/spi.o
  Compiling out/src/stm32/sdio.o
  Compiling out/src/stm32/serial.o
  Compiling out/src/generic/serial_irq.o
  Compiling out/src/stm32/hard_pwm.o
  Building out/compile_time_request.o
Too many message ids
make: *** [Makefile:84: out/compile_time_request.o] Error 255
```

markniu, 2024-04-13:
hello, you can try this https://github.com/markniu/Bed_Distance_sensor/issues/47#issuecomment-1825045187

m3hrz4d, 2024-04-14:
that fixed the issue! thank you!

Closed 2024-04-14.

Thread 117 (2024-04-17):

No data or corrupt data from BDsensor(                    ), Please check connection

Townie-au, 2024-04-17:
My setup was broken. So i had to reinstall everything.
I am having an issue with katapult not being able to access after flashing the ebb42.
So I have to flash klipper via stm32 programmer.
I connected bdsensor to the ebb42 when flashing klipper after installing bdsensor.
Now I get this error all the time.
Im using BD Sensor v1.
Everything was working including the bd sensor yesterday.
[klippy (27).log](https://github.com/markniu/Bed_Distance_sensor/files/15009506/klippy.27.log)
[printer.txt](https://github.com/markniu/Bed_Distance_sensor/files/15009519/printer.txt)

Ive checked continuity on the lead from the sensor to the board. OK
Canboard communicating via CAN0.
I just tried rolling back klipper to the previous version but no change.

Got katapult and klipper working still no chnage for bd sensor.

Townie-au, 2024-04-17:
Ive checked continuity on the lead from the sensor to the board. OK
Canboard communicating via CAN0.

Townie-au, 2024-04-18:
Is the bd sensor dead? Please help

markniu, 2024-04-18:
you can test BDsensor with the gpio on the Pi.

connect the bdsensor to the gpio on the PI like gpio17 and gpio27.

[mcu host]
serial: /tmp/klipper_host_mcu

[BDsensor]
....
scl_pin: host:gpio17
sda_pin: host:gpio27

compile and flash firmware:
https://www.klipper3d.org/RPi_microcontroller.html

https://github.com/markniu/Bed_Distance_sensor/issues/111#issuecomment-2046685001

Townie-au, 2024-04-18:
Ok.
Got it working somewhat by flashing the beta firmware.
M102 s-1 returns nothing
M102 s-6 calibrates successfully
However when I go to home z I get "Bed Distance Sensor data error:10.24"
When I first started klipper up I got "collision_homing in printer.cfg invalid". So I commented out both collison homing lines.

markniu, 2024-04-18:
Glad to hear it works again.

Townie-au, 2024-04-18:
What about this Mark?
However when I go to home z I get "Bed Distance Sensor data error:10.24"

markniu, 2024-04-18:
if M102 s-1 returns nothing or 10.24 means the same connection problem.

markniu, 2024-04-18:
did you modify the cable before or just the software?

Townie-au, 2024-04-18:
> did you modify the cable before or just the software?

Just the software.

markniu, 2024-04-18:
for finding out what's the problem hardware or software, I think you can try the gpio on the pi.

Townie-au, 2024-04-18:
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

host: Current version v0.12.0-124-g09a78c31
Up-to-date MCU(s):
<none>

Once the underlying issue is corrected, use the "RESTART"
command to reload the config and restart the host software.

mcu 'host': Unknown command: I2C_BD_send

Townie-au, 2024-04-18:
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

I connected the BD Sensor to my main board, recompiled and reflashed both EBB and M5P and got the same result. :(

markniu, 2024-04-18:
how about use the gpio in the EXP1? E.g. PB6 PB7

Townie-au, 2024-04-18:
> how about use the gpio in the EXP1? E.g. PB6 PB7

Im going to try the RPI.

Townie-au, 2024-04-18:
3.2 40 Pins GPIO
When Manta series motherboard work with CB1, 40 pins GPIO is a custom IO arrangement, as shown in the figure below, Pin 7 is CB1's "PC7", and Pin 11 is CB1's "PC14". The GPIO number of CB1 corresponds to (Px–PA)*32 + Pin
For example:
PC7 = (PC–PA)*32 + 7 = 2 * 32 + 7 = 71
PH10 = (PH–PA)*32 + 10 = 7 * 32 + 10 = 234
PC7 is numbered in Klipper as pin: host: gpio71, PH10 as pin: host: gpio234

WTH. Trying to make sense of this. I am using pin 6 and pin 8.

Townie-au, 2024-04-18:
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

Townie-au, 2024-04-18:
OMG. Finally worked it out. GPIO78 and GPIO74
Same error on CB1 GPIO.

markniu, 2024-04-18:
> OMG. Finally worked it out. GPIO78 and GPIO74 Same error on CB1 GPIO.

worked on RPI GPIO?

Townie-au, 2024-04-18:
> > OMG. Finally worked it out. GPIO78 and GPIO74 Same error on CB1 GPIO.
>
> worked on RPI GPIO?

No. Same error. No data or corrupt data from BDsensor(                    ), Please check connection

markniu, 2024-04-18:
what's the hardware version of bdsensor?

Townie-au, 2024-04-18:
> what's the hardware version of bdsensor?

How do I tell?

markniu, 2024-04-18:
there is a version text on the sensor on the other side of the white connector, like v1.3 or v1.1

Townie-au, 2024-04-18:
v1.1

markniu, 2024-04-18:
does the led on the sensor work? it will light on if it detects the metal else off.

Townie-au, 2024-04-18:
> does the led on the sensor work? it will light on if it detects the metal else off.

Yes led lights up when metal is brought nearby

markniu, 2024-04-18:
then from the hardware, we can only to find if the problem is from the dead mcu or the cable.
do you have one more cable to replace the old one for the bdsensor?

Townie-au, 2024-04-18:
> then from the hardware, we can only to find if the problem is from the dead mcu or the cable. do you have one more cable to replace the old one for the bdsensor?

No I dont. I checked the cable with the multimeter.

markniu, 2024-04-18:
if you have a solder tool you can try to connect to a serial model, there will be many useful data output from the serial com port.

Townie-au, 2024-04-18:
Do I need to open the case for that?

markniu, 2024-04-18:
> Do I need to open the case for that?

No
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

Townie-au, 2024-04-18:
Would a ST LINK work?

markniu, 2024-04-18:
> Would a ST LINK work?

No, the MCU on the v1.1 is not stm32

Townie-au, 2024-04-18:
> > Would a ST LINK work?
>
> No, the MCU on the v1.1 is not stm32

Would you be able to send me another bd sensor please?
Ill get the USB>UART converter and debug this one for you.

markniu, 2024-04-18:
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

No problem, send me an email with your shipping address.

Townie-au, 2024-04-18:
Thankyou 👍👍👍
What's your email?

markniu, 2024-04-18:
niujl123@sina.com

Townie-au, 2024-04-20:
I've sent you the email mark and I've ordered the adapter. Should get here Tuesday.
What commands do I send to retrieve the data?

markniu, 2024-04-20:
> I've sent you the email mark and I've ordered the adapter. Should get here Tuesday. What commands do I send to retrieve the data?

any serial software is ok, like pronterface.  no command needed.

Townie-au, 2024-04-20:
> > I've sent you the email mark and I've ordered the adapter. Should get here Tuesday. What commands do I send to retrieve the data?
>
> any serial software is ok, like pronterface. no command needed.

Does it need to be plugged into the printer as well or just read it straight from the sensor?

What do I need to look for?

markniu, 2024-04-20:
no need to be plugged into the printer.  there will be some message output after it is powered on, and many raw data output. then we can confirm whether this sensor works well.

Townie-au, 2024-04-25:
64▒$4▒▒▒▒▒▒▒▒▒▒▒▒▒▒▒▒▒▒yy▒4e▒▒▒G▒5▒▒▒55▒䊊▒F▒▒!!1▒▒F▒!▒▒▒▒)▒▒))▒▒▒▒▒N▒▒▒▒▒D▒5ڃ▒%!▒▒▒!▒͂▒▒!▒▒1▒▒1▒▒▒▒5▒1▒!!!▒▒▒▒▒▒▒▒▒▒▒)▒▒▒▒▒▒9▒▒9▒▒▒9▒5▒▒Ń▒▒)▒i▒▒)))9▒▒▒▒▒▒▒▒▒▒)▒▒599▒▒▒▒▒9▒)▒▒▒)▒▒%ձ45)▒▒▒▒▒▒5)▒)▒)5▒▒)▒▒▒▒5▒▒▒5)▒%▒ɱ▒▒ʂ▒▒▒)▒▒▒▒▒▒ł)▒▒▒▒▒▒▒▒▒▒)▒)D▒▒▒)))▒▒▒d▒▒▒d▒▒▒▒▒g▒)▒5▒▒)▒▒▒▒䙂▒d▒▒4▒▒▒))▒)▒)5))i▒▒)▒▒)▒▒▒▒▒▒▒▒₂▒▒▒▒䂂)▒)▒▒▒▒)▒▒▒▒▒▒▒▒ʶ▒▒▒)▒▒)▒▒▒▒▒▒▒▒▒▒▒▒)5▒▒))▒▒5▒▒ʂ▒▒)D▒▒▒▒▒▒)i▒▒▒▒▒▒▒▒5▒▒▒▒▒▒▒▒̂▒䂾5▒▒▒▒▒▒▒▒▒▒▒▒▒▒)▒

markniu, 2024-04-25:
> 64▒$4▒▒▒▒▒▒▒▒▒▒▒▒▒▒▒▒▒▒yy▒4e▒▒▒G▒5▒▒▒55▒䊊▒F▒▒!!1▒▒F▒!▒▒▒▒)▒▒))▒▒▒▒▒N▒▒▒▒▒D▒5ڃ▒%!▒▒▒!▒͂▒▒!▒▒1▒▒1▒▒▒▒5▒1▒!!!▒▒▒▒▒▒▒▒▒▒▒)▒▒▒▒▒▒9▒▒9▒▒▒9▒5▒▒Ń▒▒)▒i▒▒)))9▒▒▒▒▒▒▒▒▒▒)▒▒599▒▒▒▒▒9▒)▒▒▒)▒▒%ձ45)▒▒▒▒▒▒5)▒)▒)5▒▒)▒▒▒▒5▒▒▒5)▒%▒ɱ▒▒ʂ▒▒▒)▒▒▒▒▒▒ł)▒▒▒▒▒▒▒▒▒▒)▒)D▒▒▒)))▒▒▒d▒▒▒d▒▒▒▒▒g▒)▒5▒▒)▒▒▒▒䙂▒d▒▒4▒▒▒))▒)▒)5))i▒▒)▒▒)▒▒▒▒▒▒▒▒₂▒▒▒▒䂂)▒)▒▒▒▒)▒▒▒▒▒▒▒▒ʶ▒▒▒)▒▒)▒▒▒▒▒▒▒▒▒▒▒▒)5▒▒))▒▒5▒▒ʂ▒▒)D▒▒▒▒▒▒)i▒▒▒▒▒▒▒▒5▒▒▒▒▒▒▒▒̂▒䂾5▒▒▒▒▒▒▒▒▒▒▒▒▒▒)▒

the baud rate should be 115200

markniu, 2024-04-25:
that's the raw data from the mcu, and seems the sensor works well.

Townie-au, 2024-04-25:
> that's the raw data from the mcu, and seems the sensor works well.

So why the error in mainsail mark?

Townie-au, 2024-04-25:
> that's the raw data from the mcu, and seems the sensor works well.

I want it to work again. :(
Where do we go from here?

markniu, 2024-04-27:
I think it only to check the connection/pin number and try to increase the delay value in the BDsensor section.

Townie-au, 2024-05-12:
Hey Mark
Thank you so much for sending the new sensor.
It worked straight away. With the cable I was using before. I didn't use your one because it's too long just to go to the tool head and I didn't want to cut it.
Unless it's an intermittent thing. I'll keep you posted.
How do I use the realtime leveling?

Closed 2024-05-17.

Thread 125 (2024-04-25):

Probe goes nuts

P1t0u, 2024-04-25:
This is my probe: BDsensorVer:V1.1 pandapi3d.com ,switch_mode=0,collision_homing=0,collision_cal=0

It is connected to the BL Touch port on a BTT Manta M5P
[BDsensor]
sda_pin: PC13
scl_pin: PC15
delay: 20
x_offset: -33
y_offset: 0
no_stop_probe:
position_endstop: 0.5
collision_homing:0
collision_calibrate:0

KLIPPER and the bed sensor code were updated on Apr 16, the MCU was reflashed  at that time.  This has been going on since I installed the probe about a month ago.

It will work for a while then it says it is triggered when it is clearly not.

M119
x:open y:open z:open
G28 Z
triggered at 10.150 mm
warning:triggered at 0mm, Please slow down the homing z speed
Z triggered at 0.000 mm,auto adjusted.
M119
x:open y:open z:open

The probe is actually about 120MM from the bed and the LED is OFF

I will then power cycle the printer and all is good for a while; then it will go nuts again

markniu, 2024-04-26:
did you calibrate the bdsensor? and what's the data returned after M102 S-5 ?

P1t0u, 2024-04-26:
Yes I ran M102 S-6, here is the M102 S-5 data:
1015
1015
1015
1015
1015
976
976
976
964
943
921
902
880
857
837
817
794
770
749
727
704
681
661
640
614
589
565
541
517
492
469
444
419
369
369
345
315
287
262

The probe is about 2mm from the tip of the nozzle, I tried making the gap smaller in order to get closer to 100 for the first reading but then I did not have 10 between the first and second values.

G1 Z1
BDSENSOR_DISTANCE
1.02mm

markniu, 2024-04-27:
you can add `homing_retract_dist:0` in the section stepper_z.
and also attach klipply.log

P1t0u, 2024-04-27:
As requested I added homing_retract_dist:0 in my configuration, a few minutes later I changed the filament in the printer and upon loading the new filament I had the error which I confirmed with:
G28 Z
triggered at 10.030 mm
warning:triggered at 0mm, Please slow down the homing z speed
Z triggered at -0.120 mm,auto adjusted.

The probe is 180mm from the bed and M119 correctly reports x:open y:open z:open

I am attaching klippy.log
[klippy-5.log](https://github.com/markniu/Bed_Distance_sensor/files/15139166/klippy-5.log)

markniu, 2024-04-28:
what's the returned value after M102 S-2 instead of M119, it seems the returned value is -0.12

markniu, 2024-04-28:
I also suspect the electrinic noise from other wires for example the motor or heater.
could you try the
G28 Z
G28 Z

P1t0u, 2024-04-28:
G28
triggered at 10.150 mm
warning:triggered at 0mm, Please slow down the homing z speed
Z triggered at 0.000 mm,auto adjusted.
M119
x:open y:open z:open
M102 S-2
BDsensor:Out of measure Range or too close to the bed

Sadly M102 S-2 is useless in this case.

Further testing allowed me to get the error on demand, every time I loaded or unloaded the filament I could not home Z properly.  Right now I am at the point where it seems that the probe cable does not like running in the cable chain alongside the extruder stepper motor cable (I have run many print jobs successfully so I don't think the hot end is involved, the extruder stepper motor gets to spin faster while loading and unloading the filament so that is my number one suspect).  I have installed another cable on the outside of the cable chain and went from 100% failures to 0%.  The sampling is still pretty small so I won't call it solved just yet but it looks much better.

Now I need to figure out a permanent way to affix the probe cable on the outside of the cable chain.

markniu, 2024-04-29:
someone also report this electromagnetic interference recently, so now I just updated the new cable back to the same as first version  bdsensor, that is shielded, twisted pairs and high purity copper wire for preventing EMI. it will be shipped with the bdsensor now instead of the old cables in the stock.
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

P1t0u, 2024-04-29:
That sounds really nice…. Can I have one?

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

markniu, 2024-04-30:
> That sounds really nice…. Can I have one?
yes, please send me your shipping address to my email: niujl123@sina.com

lunatec84, 2024-05-08:
I’ve got the same errors and it’s not the 30mm long cable to the Toolboard of my printer! Meanwhile I’ve ruined 2 Bondtech CHT nozzles, the second 350x350mm not so cheap CR3D PEI flex-plate and wasted about 65€ filament with this sensor! Now this sensor looks like really bad beta crap to me. Three month ago, there are a lot of bugs with CAN toolboard timer to close error messages and false z value readings, I’ve ruined the first PEI flex-plate and switched back to quickdraw probe. Yesterday I gave this sensor another try, flashed the firmware to the v1.3 sensor, and compiled and flashed Klipper on the EBB36 using CAN speed at 1M. Calibrated the probe, scratched the bed with the nozzle while doing a QGL (bug), printed 3 parts with perfect first layers and then, I’m getting the same timer to close error after 6,5 hours and 75% finished print, wasting 640g Fiberlogy PA12CF15. With the collision probing, the first 5 attempts were okay and at the 6. attempt, the nozzle crashed hardly into the printbed and ruined with the force of the 4 Z motors, parts from the quad gantry and toolhead. I’m totally pissed off with this crap buggy sensor. With the quickdraw probe QGL was fine, why the heck is your code when doing a QGL, moving at first z down in the center of the bed and moving in this low height to the QGL corner points and scratching the unleveled bed with the nozzle, instead of moving to a safe z height, moving to the first corner point, measuring, moving z back to save height and doing the 3 remaining gantry level points in the same way? That wasn’t the case with earlier versions. Heaters where off during probing, because it gives me false sensor readings and sensor calibration values where also okay on the four calibration attempts I’ve tried. With the money I’ve wasted meanwhile in destroyed parts from this crap sensor usage,  I’ve could bought 4-5 out of the box working beacon sensors! I don’t think that it is a good idea to include this buggy sensor and code in klipper at this time.

markniu, 2024-05-08:
I am so sorry for that waste and thank you for the support and feedback those helpful information.
the timer too close should be the new bug caused by the recent code committed that I have not test too much.
and about the QGL there is a new quad_gantry_level_probe:1  that can let the probe up and down while doing QGL.

lunatec84, 2024-05-08:
In January 2024, I also encountered issues where the timer to close error appeared with this sensor. Even with your code patched into Klippy, the error occurred intermittently when the sensor wasn't in use. This isn't a new bug, and I'm not the only one experiencing these errors. Today, I've reduced the power, speed, and acceleration for Z-axis movements to prevent further damage caused by sensor or code failures. However, the QGL problem persists despite enabling QGL collision probing. The code needs to be adjusted to include a configurable save Z height variable for movements between QGL points, as a belt-driven gantry can unevenly move 10-20mm when stepper motors get unpowered, potentially causing damage to the printer bed or other components. Additionally, the QGL code seems to ignore given z_hop values. Another issue I encountered today was a Toolboard MCU move queue overflow in mid-print. I suspect that sensor data is overloading the CAN bus even at 1Mbit on a fast printer. Moreover, the sensor occasionally triggers in mid-air, and its LED flickers when it's in the triggered range. It's possible that my sensor is faulty. I’m thinking about opening the sensor housing and connecting the analog pin from the sensor chip to an oscilloscope for further analysis. It would also be helpful if you could provide another sensor for testing. At some points I was near to the trash bin with this sensor or making a video from the actual status and a report, but the only thing beware me from that, is the point that if it worked correctly some times, it’s doing a really good job and i would see this sensor in the official klipper repo soon, but for now there are definitely too much and too heavy bugs for including it. I would give you further informations, feedback and helping you to get this sensor reliable, because I know that it’s not an easy task, especially when real-time comes into play.

markniu, 2024-05-08:
Thank you so much for far more test , please send me your shipping address with email:niujl123@sina.com, I would like to send you the 2 type of new sensor for test.

> In January 2024, I also encountered issues where the timer to close error appeared with this sensor. Even with your code patched into Klippy, the error occurred intermittently when the sensor wasn't in use. This isn't a new bug, and I'm not the only

Closed 2024-06-09.

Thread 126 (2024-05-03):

Klipper calibration issue

dhoard, 2024-05-03:
I had to rebuild my Klipper machine, so I needed to recalibrate the printer/BDsensor.

I ran through the [instructions](https://github.com/markniu/Bed_Distance_sensor/wiki/Installing-for-Klipper ) and found that I had issues at [step 5](https://github.com/markniu/Bed_Distance_sensor/wiki/Installing-for-Klipper#5-calibration).

"Send command SET_KINEMATIC_POSITION Z=50  then move the Z axis down in the menu until the nozzle just touches the bed plate, the BDsensor will use this position as the zero position."

If the toolhead is located further than 50mm above the print plate when issuing the command, then Klipper wouldn't allow enough Z movement to move the nozzle down to "just touch the bed."

```
Move out of range: 0.000 0.000 -.100 [0.000]
```

I worked around the issue by...

1. disabling the steppers in Klipper
2. manually rotating the Z lead screw(s) so that the nozzle "just touches the bed."
3. issuing `SET_KINEMATIC_POSITION Z=0`
4. continue with the remaining calibration instructions

Post-calibration tests seem correct.

Thoughts on changing the instructions?

markniu, 2024-05-04:
seems the 50mm is not enough, you can set it to 200, `SET_KINEMATIC_POSITION Z=200`  I also have updated that in the instruction.

Closed 2024-05-04.

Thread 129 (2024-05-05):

Homing X or Y causes Z to appear as though it was homed

markleaf131313, 2024-05-05:
Whenever I home X or Y independently the Z automatically becomes homed as well, though it never did the homing.

When I turn off the motors (M84) it crashes with the error "MCU 'host' shutdown: Invalid oid type". I am using sensorless homing and have the homing overriden with the gcode below and in the console BDsensor I guess outputs the leveling height.

```
Klipper state: Shutdown
Real time leveling height:0.000000
M84
```

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

```
[gcode_macro _HOME_X]
gcode:
    # Always use consistent run_current on A/B steppers during sensorless homing
    {% set RUN_CURRENT_X = printer.configfile.settings['tmc2209 stepper_x'].run_current|float %}
    {% set RUN_CURRENT_Y = printer.configfile.settings['tmc2209 stepper_y'].run_current|float %}
    {% set HOME_CURRENT = 0.7 %}
    SET_TMC_CURRENT STEPPER=stepper_x CURRENT={HOME_CURRENT}
    SET_TMC_CURRENT STEPPER=stepper_y CURRENT={HOME_CURRENT}
    SAVE_GCODE_STATE NAME=STATE_HOME_X

    # Home
    G28 X
    # Move away
    G91
    G1 X65 F1200

    # Wait just a second… (give StallGuard registers time to clear)
    G4 P500
    # Set current during print
    SET_TMC_CURRENT STEPPER=stepper_x CURRENT={RUN_CURRENT_X}
    SET_TMC_CURRENT STEPPER=stepper_y CURRENT={RUN_CURRENT_Y}
    RESTORE_GCODE_STATE NAME=STATE_HOME_X

[gcode_macro _HOME_Y]
gcode:
    # Set current for sensorless homing
    {% set RUN_CURRENT_X = printer.configfile.settings['tmc2209 stepper_x'].run_current|float %}
    {% set RUN_CURRENT_Y = printer.configfile.settings['tmc2209 stepper_y'].run_current|float %}
    {% set HOME_CURRENT = 0.7 %}
    SET_TMC_CURRENT STEPPER=stepper_x CURRENT={HOME_CURRENT}
    SET_TMC_CURRENT STEPPER=stepper_y CURRENT={HOME_CURRENT}
    SAVE_GCODE_STATE NAME=STATE_HOME_Y

    # Home
    G28 Y
    # Move away
    G91
    G1 Y-75 F1200

    # Wait just a second… (give StallGuard registers time to clear)
    G4 P500
    # Set current during print
    SET_TMC_CURRENT STEPPER=stepper_x CURRENT={RUN_CURRENT_X}
    SET_TMC_CURRENT STEPPER=stepper_y CURRENT={RUN_CURRENT_Y}
    RESTORE_GCODE_STATE NAME=STATE_HOME_Y

[homing_override]
axes: xyz
set_position_z: 0
gcode:
    {% set home_all = 'X' not in params and 'Y' not in params and 'Z' not in params %}
    SAVE_GCODE_STATE NAME=STATE_HOME_OVERRIDE

    {% if home_all or 'X' in params %}
        _HOME_X
    {% endif %}

    {% if home_all or 'Y' in params %}
        _HOME_Y
    {% endif %}

    {% if home_all or 'Z' in params %}
        G28 Z
    {% endif %}

    RESTORE_GCODE_STATE NAME=STATE_HOME_OVERRIDE
```

markleaf131313, 2024-05-06:
My mistake I see where it is setting the Z now.

Closed 2024-05-06.

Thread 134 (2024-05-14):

make command error

ibrahimhakkicandan, 2024-05-14:
when i try to make command with bdsensor installed it gives "Too many message ids
make: *** [Makefile:84: out/compile_time_request.o] Error 255"

Here is the full log:

pi@mainsail:~/klipper $ make
  Creating symbolic link out/board
  Building out/autoconf.h
  Compiling out/src/sched.o
  Compiling out/src/command.o
  Compiling out/src/basecmd.o
  Compiling out/src/debugcmds.o
  Compiling out/src/initial_pins.o
  Compiling out/src/gpiocmds.o
  Compiling out/src/stepper.o
  Compiling out/src/endstop.o
  Compiling out/src/trsync.o
  Compiling out/src/adccmds.o
  Compiling out/src/spicmds.o
  Compiling out/src/sdiocmds.o
  Compiling out/src/i2ccmds.o
  Compiling out/src/pwmcmds.o
  Compiling out/src/buttons.o
  Compiling out/src/tmcuart.o
  Compiling out/src/neopixel.o
  Compiling out/src/pulse_counter.o
  Compiling out/src/lcd_st7920.o
  Compiling out/src/lcd_hd44780.o
  Compiling out/src/spi_software.o
  Compiling out/src/i2c_software.o
  Compiling out/src/thermocouple.o
  Compiling out/src/sensor_adxl345.o
  Compiling out/src/sensor_angle.o
  Compiling out/src/sensor_mpu9250.o
  Compiling out/src/sensor_lis2dw.o
  Compiling out/src/sensor_ldc1612.o
  Compiling out/src/sensor_bulk.o
  Compiling out/src/BD_sensor.o
  Compiling out/src/stm32/watchdog.o
  Compiling out/src/stm32/gpio.o
  Compiling out/src/stm32/clockline.o
  Compiling out/src/stm32/dfu_reboot.o
  Compiling out/src/generic/crc16_ccitt.o
  Compiling out/src/generic/armcm_boot.o
  Compiling out/src/generic/armcm_irq.o
  Compiling out/src/generic/armcm_reset.o
  Compiling out/src/../lib/stm32f4/system_stm32f4xx.o
  Compiling out/src/stm32/stm32f4.o
  Compiling out/src/generic/armcm_timer.o
  Compiling out/src/stm32/gpioperiph.o
  Compiling out/src/stm32/adc.o
  Compiling out/src/stm32/i2c.o
  Compiling out/src/stm32/spi.o
  Compiling out/src/stm32/sdio.o
  Compiling out/src/stm32/usbotg.o
  Compiling out/src/stm32/chipid.o
  Compiling out/src/generic/usb_cdc.o
  Compiling out/src/stm32/hard_pwm.o
  Building out/compile_time_request.o
Too many message ids
make: *** [Makefile:84: out/compile_time_request.o] Error 255

if i uninstal with the script provided, the make command runs succesfully
printer: ender 3 s1 pro
make menuconfig:
Enable extra low-level configuration options not checked
Micro-controller Architecture (STMicroelectronics STM32)
 Processor model (STM32F401)
 Bootloader offset (64KiB bootloader)
Communication interface (USB (on PA11/PA12))

markniu, 2024-05-15:
Hello, you can fix this like this https://github.com/markniu/Bed_Distance_sensor/issues/47#issuecomment-1825045187
this is a problem in klipper for that there is only a few ids left now. I am trying to reduce the ids numbers that used by the sensor and will update that to github next.

ibrahimhakkicandan, 2024-05-16:
Thanks it resolved the issue.

ibrahimhakkicandan, 2024-05-16:
Thanks it resolved the issue.

Closed 2024-05-16.

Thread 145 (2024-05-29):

mcu 'EBBCan': Unknown command: I2CBD

terri1769, 2024-05-29:
I just had to uninstall and reinstall Klipper to fix a "dirty" issue.  I installed Klipper with KIAUH then went through the install steps for BDSensor.

~/Bed_Distance_sensor/klipper/install_BDsensor.sh
cd ~/klipper/
make menuconfig
./make_with_bdsensor.sh
make flash

When I try to start Klipper I get:
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

I thought it might be issue 140 but the solution doesn't work and I don't currently have a "dirty" config.

terri1769, 2024-05-30:
[klippy.log](https://github.com/markniu/Bed_Distance_sensor/files/15501979/klippy.log)

markniu, 2024-05-30:
was there a message `out/src/BD_sensor.o` on the SSH while run make_with_bdsensor.sh?

This error is from the firmware of mcu, and the code of BD_sensor.c does not build into the firmware.

terri1769, 2024-05-30:
Yes.  I built it using those instructions for the Octopus Max EZ board and
then for the EBB36 board then flashed it to each after it was built for
that device.  Here's the text of doing so for the EBB36.

***@***.***:~/klipper $ ./make_with_bdsensor.sh
compiling BD_sensor.c into the klipper firmware
  Creating symbolic link out/board
  Building out/autoconf.h
  Compiling out/src/sched.o
  Compiling out/src/command.o
  Compiling out/src/basecmd.o
  Compiling out/src/debugcmds.o
  Compiling out/src/initial_pins.o
  Compiling out/src/gpiocmds.o
  Compiling out/src/stepper.o
  Compiling out/src/endstop.o
  Compiling out/src/trsync.o
  Compiling out/src/adccmds.o
  Compiling out/src/spicmds.o
  Compiling out/src/i2ccmds.o
  Compiling out/src/pwmcmds.o
  Compiling out/src/buttons.o
  Compiling out/src/tmcuart.o
  Compiling out/src/neopixel.o
  Compiling out/src/pulse_counter.o
  Compiling out/src/lcd_st7920.o
  Compiling out/src/lcd_hd44780.o
  Compiling out/src/spi_software.o
  Compiling out/src/i2c_software.o
  Compiling out/src/thermocouple.o
  Compiling out/src/sensor_adxl345.o
  Compiling out/src/sensor_angle.o
  Compiling out/src/sensor_mpu9250.o
  Compiling out/src/sensor_lis2dw.o
  Compiling out/src/sensor_ldc1612.o
  Compiling out/src/sensor_bulk.o
  Compiling out/src/BD_sensor.o
  Compiling out/src/stm32/watchdog.o
  Compiling out/src/stm32/gpio.o
  Compiling out/src/stm32/clockline.o
  Compiling out/src/stm32/dfu_reboot.o
  Compiling out/src/generic/crc16_ccitt.o
  Compiling out/src/generic/armcm_boot.o
  Compiling out/src/generic/armcm_irq.o
  Compiling out/src/generic/armcm_reset.o
  Compiling out/src/generic/timer_irq.o
  Compiling out/src/stm32/stm32f0_timer.o
  Compiling out/src/stm32/stm32g0.o
  Compiling out/src/stm32/gpioperiph.o
  Compiling out/src/stm32/stm32f0_adc.o
  Compiling out/src/stm32/stm32f0_i2c.o
  Compiling out/src/stm32/spi.o
  Compiling out/src/generic/canserial.o
  Compiling out/src/../lib/fast-hash/fasthash.o
  Compiling out/src/stm32/fdcan.o
  Compiling out/src/generic/canbus.o
  Compiling out/src/stm32/chipid.o
  Compiling out/src/stm32/hard_pwm.o
  Building out/compile_time_request.o
Version: v0.12.0-207-g6cd17420
  Preprocessing out/src/generic/armcm_link.ld
  Linking out/klipper.elf
  Creating hex file out/klipper.bin
Updated 1 path from the index
Updated 1 path from the index

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

markniu, 2024-05-31:
you still can run the make instead of ./make_with_bdsensor.sh after install_BDsensor.sh, then you can see if the firmware is flashed success into the EBBcan by seeing if there is text dirty on the version page
```
~/Bed_Distance_sensor/klipper/install_BDsensor.sh
cd ~/klipper/
make menuconfig
make
make flash
```

aldoale, 2024-05-31:
I have the same error

Magoo007, 2024-05-31:
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
Same errore, the solution here and also in topic #140 doesn’t fix it

markniu, 2024-05-31:
please use the old methond to compile:
```
~/Bed_Distance_sensor/klipper/install_BDsensor.sh
make
```
then if the compile and flash goes well there should be a dirty and compile date in the MCU version text.

Life0fBrian, 2024-05-31:
I can confirm that this works!
Just install the bd_sensor patch and properly flash the EBB36.

terri1769, 2024-05-31:
No idea what I did differently this time but it appears to be working now.  Thank you.

GromovPeter, 2024-06-08:
hi
mcu 'mcu': Unknown command: I2CBD

root@K1C-5D0B /usr/data/klipper [#] sh ./make_with_bdsensor.sh
compiling BD_sensor.c into the klipper firmware
make: avr-gcc: Command not found
  Compiling out/src/sched.o
/bin/sh: avr-gcc: not found
make: *** [Makefile:65: out/src/sched.o] Error 127
Updated 1 path from the index
Updated 1 path from the index

what can i do to fix it ?

markniu, 2024-06-09:
seems you have not `make menuconfig` to choose the right mcu type.

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

GromovPeter, 2024-06-09:
how to know mcu type of k1c ?

McMark1441, 2024-07-13:
I have the same issue. Currently running Octopus in USB Can bridge to my EBB SB2209. I've been working on this for a week with no luck. Flashed, Re-flashed, updated all boards involved.

McMark1441, 2024-07-14:
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

@terri1769 Please mark this as the solution.

Seems like you have to run the commands in the following order:

```shell
cd ~/klipper
make clean
make menuconfig
~/Bed_Distance_ sensor/klipper/install_BDsensor.sh
make
```
Put you tool head into DFU mode, then
```shell
make flash FLASH_DEVICE=XXXX:XXXX
```

terri1769, 2024-07-14:
Resolved

bombsquad85, 2024-08-29:
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

This didnt work for me. well, not completely. this got rid of the red MCU error, however when i went to test the bd sensor it said there was an error

bombsquad85, 2024-08-29:
when i follow the directions above, i get rid of the red screen errors, however when i check the connection to the BD sensor i get this: 11:15 PM
No data or corrupt data from BDsensor(                    ), Please check connection
11:15 PM
M102 S-1
11:14 PM
Bed Distance Sensor data error2:10.24

markniu, 2024-08-29:
check the hardware first, which board and pins do you use?

> when i follow the directions above, i get rid of the red screen errors, however when i check the connection to the BD sensor i get this: 11:15 PM No data or corrupt data from BDsensor(��������������������), Please check connection 11:15 PM No data or corrupt data from BDsensor(��������������������), Please check connection 11:15 PM M102 S-1 11:14 PM Bed Distance Sensor data error2:10.24 11:14 PM M119

leftouterjoins, 2024-11-09:
I can confirm the steps as outlined by @McMark1441 solve this issue

terri1769, 2024-11-09:
Resolution here:  https://github.com/markniu/Bed_Distance_sensor/issues/145#issuecomment-2316610804

Closed 2024-11-09.

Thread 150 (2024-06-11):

Real Time update fail: update z must be >0

Townie-au, 2024-06-11:
BDsensorVer:V1.2c pandapi3d ,switch_mode=1,collision_homing=1,collision_cal=1

About a minute into the print, halts printer.

Townie-au, 2024-06-11:
[
[logs-20240611-154328.zip](https://github.com/user-attachments/files/15782830/logs-20240611-154328.zip)
](url)

markniu, 2024-06-11:
here the actual error is the timer too close, and I will change this message `fail: update z must be >0 ` as a warning message later.
you can add `rt_sample_time:20 ` into the BDsensor section,here 20 means the distance reading sample time is 20ms.
The value of rt_sample_time depends on the MCU speed, it should be higher if the MCU speed is lower.

Townie-au, 2024-06-18:
Different error this time
[Uploading klippy.log (13).txt…]()

markniu, 2024-06-18:
Seems the klippy.log file was not updated successfully.
> Different error this time Uploading klippy.log (13).txt…

Townie-au, 2024-06-18:
CPU: Allwinner H616, Quad-core Cortex-A53 @1.5GHz

markniu, 2024-06-18:
> Different error this time Uploading klippy.log (13).txt…

could you update the klippy.log file again?  and I cann't download this file

Townie-au, 2024-06-18:
[klippy.log (13).txt](https://github.com/user-attachments/files/15884429/klippy.log.13.txt)

markniu, 2024-06-18:
did the error " Unable to read tmc uart 'stepper_z' register GSTAT" happen in the first layer?

Townie-au, 2024-06-18:
Yes

Townie-au, 2024-06-18:
BD sensor and klipper were out of date.
I updated it this morning. I'll give it another go when I get home.

markniu, 2024-06-19:
> did the error " Unable to read tmc uart 'stepper_z' register GSTAT" happen in the first layer?

and I think this should be the same as the error `timer too close`, you can adjust the the `rt_sample_time: ` to 25 or 30

Townie-au, 2024-06-19:
What does this mean?

Real Time update fail: update z must be >0

3:45 PM

Real time leveling height:0.20 ( 0.20 z_offset:0.00)

Andrew

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

Townie-au, 2024-06-19:
[klippy.log (14).txt](https://github.com/user-attachments/files/15896216/klippy.log.14.txt)

Townie-au, 2024-06-19:
On the bottom of printer.cfg it has this

747 #*# [BDsensor]

748 #*# z_adjust = 0.0

749 #*# z_offset = 0

Townie-au, 2024-06-19:
So changing rt_sample_time: to 30. Seems to have worked but still getting the real time update fail error in the console but print continuing.

markniu, 2024-06-19:
> What does this mean? Real Time update fail: update z must be >0 3:45 PM Real time leveling height:0.20 ( 0.20 z_offset:0.00)
that means it will not adjust the z height while printing because the current z position is <0 or higher than setting value

markniu, 2024-06-19:
> > What does this mean? Real Time update fail: update z must be >0 3:45 PM Real time leveling height:0.20 ( 0.20 z_offset:0.00)
>
> that means it will not adjust the z height while printing because the current z position is <0 or higher than setting value

I have changed this message, and this message is normal sometimes because the z maybe changed in the first layer,for example the intro line in the start gcode in the slicer or retraction

Townie-au, 2024-06-19:
Nope. Shutdown 6% in timer too close EBBCan
[klippy.log (15).txt](https://github.com/user-attachments/files/15899128/klippy.log.15.txt)

markniu, 2024-06-19:
> Nope. Shutdown 6% in timer too close EBBCan [klippy.log (15).txt](https://github.com/user-attachments/files/15899128/klippy.log.15.txt)

did it happen in the first layer? if not make sure there is a `BDSENSOR_SET REAL_TIME_HEIGHT=0` after first layer in the gcode file to disable this feature?

Townie-au, 2024-06-19:
Yeah that's what I thought. I have that gcode in already.
I'll try it with a bed mesh and see how it goes.

feral42, 2024-07-31:
any updates on this?  I'm having the same problem.

Townie-au, 2024-08-01:
I managed to get real time levelling working.

I didnt remove all bed mesh related sections in my printer.cfg and I changed rt_sample_time to 16ms.

Closed 2024-08-01.

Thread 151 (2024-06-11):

Error no data

alhanon, 2024-06-11:
after connect sensor to board but sensor information no data this problem after I change main board for printer back to old one same problem no data check wiring but its OK read light working I use BDsensorM

No data or corrupt data from BDsensor( ), Please check connection

markniu, 2024-06-12:
is there a EXP1 connector on the main board? and recommend to use the EXP1

alhanon, 2024-06-12:
no I use skr pico

markniu, 2024-06-12:
which ports and gpio do you use? some of the ports  on that board can not be used as gpio,for example there are signal filter on the endstop pins that will do filter the communication signal.

markniu, 2024-06-12:
or you can use the gpios on the pi if you use rasspberrypi as the host.

alhanon, 2024-06-12:
I use this gpios before and its work but I remove it to anther printer not work back it to original one not work I think its broken

[BDsensor]

sda_pin: gpio22 # example of connecting to main board Creality V4.2.7
scl_pin: gpio29
delay: 20 # 20us per pulse, this value should be >=18 but must be below 30
#z_offset:0 #  within -0.6 to 0.6mm
#z_adjust: -0.02
x_offset: -34
y_offset: 0
no_stop_probe: # fast probe that the toolhead will not stop at the probe point,disable it by commenting out.
position_endstop: 0.5 #the Z axis will be triggered after it measured the distance is below this value(mm) while homing z, recommend value is 0.5~1.0
speed:0.8 # this speed only works for the z tilt and PROBE_ACCURACY command.
collision_homing:0 #  set it 1 to enable homing with nozzle collision sensing.
collision_calibrate:0 # set it 1 to enable auto calibrate BDsensor with nozzle collision sensing.
[force_move]
enable_force_move: true

markniu, 2024-06-12:
normally, the chip on the sensor will be very hot if it is broken, for example the 5V and GND are invert.
and does the led on the sensor work?

alhanon, 2024-06-12:
It normally not hot . The led work if near bed like normally

alhanon, 2024-06-12:
Flash the firmware normally without problem
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

markniu, 2024-06-13:
what's the cable for the BDsensor? I found a few of the old 5 color cables can also cause the connection problem even passed test with multimeter.

alhanon, 2024-06-13:
not cable I change it 3 times .
I lost my hope to work again

Thank you

Closed 2024-06-21.

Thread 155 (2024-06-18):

Internal error on command:"BED_MESH_CALIBRATE"

legacy23, 2024-06-18:
Hello @markniu

I am not able to complete Bed Mesh.  Keep getting error "Internal error on command:"BED_MESH_CALIBRATE"" with a "'NoneType' object is not subscriptable" and klipper shutdowns when this happens.   Here is my config and klippy.log

M102 S-1  BDsensorVer:V1.2bpandapi3d.com ,switch_mode=1,collision_homing=1,collision_cal=1

// 1015
// 1015
// 1015
// 1015
// 1015
// 1015
// 1015
// 956
// 956
// 956
// 956
// 949
// 934
// 915
// 892
// 856
// 849
// 825
// 802
// 776
// 751
// 725
// 698
// 673
// 645
// 621
// 593
// 569
// 545
// 520
// 496
// 472
// 449
// 426
// 404
// 382
// 361
// 340
// 320
// 308
$ M102 S-5

[stepper_z]
step_pin: PB6
dir_pin: !PB5
enable_pin: !PC3
microsteps: 16
rotation_distance: 8
#endstop_pin: ^PA7
endstop_pin: probe:z_virtual_endstop
#position_endstop: 0.0
#position_max: 250
position_max: 300
position_min: -8
homing_speed: 5
second_homing_speed: 1  #set this to 3 if homing with collision
homing_retract_speed: 20
homing_retract_dist: 3

[BDsensor]
sda_pin: PB1
scl_pin: PB0
delay: 10
z_offset: -0.6
z_adjust: -0.3
x_offset: -45
y_offset: -7
#no_stop_probe:
position_endstop: 2.0
speed: 0.8
collision_homing: 1
collision_calibrate: 1

[bed_mesh]
speed: 120
mesh_min: 30,30
mesh_max: 200,210
probe_count: 6,6
horizontal_move_z: 1
algorithm: bicubic
zero_reference_position: 115,115

[klippy.log](https://github.com/user-attachments/files/15880954/klippy.log)

markniu, 2024-06-18:
Hello, you can remove the` #` which is in front of the `no_stop_probe:`

legacy23, 2024-06-19:
Thanks Mark, finally got a my Mesh, I thought “no_stop_probe” was optional.

I am still having a hard time setting the z_offset,  to get a good first layer I am required to have around 1mm or more and z_offset allows only  0.6mm.

Is the firmware 1.2c required to for it to auto z_offset?

markniu, 2024-06-20:
hello, you can try this: add position_min : 0 in the stepper_z section
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

markniu, 2024-06-20:
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

 this “no_stop_probe” is optional now, and I fixed it by sync the code from the latest official klipper.

it should no need to set the z_offset and recommend to keep it to 0 if you have enabled the collision_homing,

Closed 2024-06-26.

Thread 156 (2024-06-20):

G28 Failure BedMeshCalibrate' object has no attribute '_get_adjusted_points

creek52, 2024-06-20:
I followed the WIKI Install and everything worked until  Step 7.
I started with a fresh install of Klipper with Fluiid using KIAUH on a Pi3b to talk to a Creality 4.2.7 board. Everything was updated to current . Worked fine with BLTouch probe. Then converted to BD Sensor.
Created new firmware file using './make_with_bdsensor.sh', new bin file was slightly larger than previous bin file. It flashed to the board correctly.
I connected and was able to confirm  sensor is BDsensorVer:V1.2 pandapi3d.com ,switch_mode=0,collision_homing=0,collision_cal=0
I was able to read head distance from bed correctly and calibration data was returned properly.
G28 failed in Step 7.  Attached part of klippy.log and printer.cfg.

I looked at the one issue with a G28 problem and I have no aliases defined any where. That wasn't it.

Thanks.

[BD Sensor V1.2 Problem.txt](https://github.com/user-attachments/files/15917496/BD.Sensor.V1.2.Problem.txt)

markniu, 2024-06-21:
the reason was the official klipper modified the probe code yesterday, and I also sync it into BDsensor.py, please update the BDsensor.py again.

markniu, 2024-06-21:
> the reason was the official klipper modified the probe code yesterday, and I have sync it into BDsensor.py, please update the BDsensor.py again.

creek52, 2024-06-21:
Many Thanks, it has fixed the problem.

Closed 2024-06-21.

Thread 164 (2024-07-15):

Trouble Adding BD Sensor to Ender 3 Pro with SKR PRO V1.2

Haxim, 2024-07-15:
Struggling to figure out what I'm doing wrong, I feel like I'm so close

Compiling Marlin 2.1.x-bugfix (current as of a few days ago)
Everything is connected correctly (LED on BD Sensor behaves properly when close to metal)
M102 doesn't return as expected (no mention of V1.0 pandapi3d.com):
```
>>> M102 S-1
SENDING:M102 S-1
ok P15 B3
```
M119 behaves oddly. z_min changes from open to TRIGGERED, but z_probe is always set to triggered (I would expect probe to change and z_min to always stay the same)
```
SENDING:M119
Reporting endstop status
x_min: open
y_min: open
z_min: open
z_probe: TRIGGERED
```
M102 S-6 behaves correctly and calibrates, M102 S-5 reads back the calibration curve
Board is a BTT SRK PRO V1.2 (pinouts https://github.com/bigtreetech/BIGTREETECH-SKR-PRO-V1.1/blob/master/SKR-PRO-V1.2/manual/SKR-PRO-V1.2PIN.PDF)

I've set the following pins (used to have a BL Touch installed, so the BD Sensor is just using the same connection on the hotend)
```
#ifndef I2C_BD_SDA_PIN
  #define I2C_BD_SDA_PIN                 PA2
#endif

#ifndef I2C_BD_SCL_PIN
  #define I2C_BD_SCL_PIN                 PA1
#endif

#ifndef I2C_BD_DELAY
  #define I2C_BD_DELAY                   20
#endif

```
Not sure why M102 S-1 isn't responding and z-probe isn't updating correctly. Any ideas?

markniu, 2024-07-15:
for testing, you can then try to  connect to the EXP1, for example  LCD_D7_PG7 and  LCD_D7_PG6 for the SDA and SCL

Haxim, 2024-07-16:
> for testing, you can then try to connect to the EXP1, for example LCD_D7_PG7 and LCD_D7_PG6 for the SDA and SCL

same behaviour (z_min changes state instead of z_probe) on PG7 and PG6 (EXP1 ports suggested for this board). I'm wondering if it's a weird Marlin issue, going to try a different version of the bugfix branch and see if that resolves it.

markniu, 2024-07-16:
did you enable the` USE_PROBE_FOR_Z_HOMING` ?
```
//#define Z_MIN_PROBE_USES_Z_MIN_ENDSTOP_PIN
// Force the use of the probe for Z-axis homing
#define USE_PROBE_FOR_Z_HOMING
```
and you can this firmware that I pulled to official marlin recently.
https://github.com/markniu/MarlinPULL/tree/bugfix-2.1.x
https://github.com/MarlinFirmware/Marlin/pull/27243

Haxim, 2024-07-19:
Yep, I have using the endstop commented out and use probe for homing
I'll give your fork a shot! Does it also support nozzle collision sensing for Marlin?

markniu, 2024-07-19:
the code on my github supports the collision sensing.

Haxim, 2024-07-19:
Great! I just tried a quick build with your fork and m102 S-1 correctly reports
```
ok P15 B3
BD Sensor version:V1.2c pandapi3d
,sw_mode:1
```
Which seems better than I had before. Now I just need to redo my configurations for this version. Thanks!

Haxim, 2024-07-20:
Works great after setting up my config. Appreciate all the help @markniu

Closed 2024-07-20.

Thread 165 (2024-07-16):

Trouble adding to ramps1.4 board

peterstevey, 2024-07-16:
I've added the bd sensor to my project build but having issues getting the sensor to work correctly.

M102 S-1 doesn't return as expected (no mention of V1.0 pandapi3d.com):

>>> M102 S-1
SENDING:M102 S-1
ok

Calibration works fine, and the mesh is saved without problem.

Endpoint is not triggered, and distance is not displayed on LCD.

Software is configured exactly as outlined in Chris's Basement tutorial and on the github documentation.

Changing pins doesnt seem to help. Would updating the bdsensor firmware affect this?

Calibration data seems good, although have little benchmark to compare to.
SENDING:M102 S-5
Calibrate data:0,202, check:1
Calibrate data:1,229, check:1
Calibrate data:2,258, check:1
Calibrate data:3,287, check:1
Calibrate data:4,318, check:1
Calibrate data:5,347, check:1
Calibrate data:6,377, check:1
Calibrate data:7,407, check:1
Calibrate data:8,438, check:1
Calibrate data:9,468, check:1
Calibrate data:10,497, check:1
Calibrate data:11,524, check:1
Calibrate data:12,553, check:1
Calibrate data:13,579, check:1
Calibrate data:14,606, check:1
Calibrate data:15,628, check:1
Calibrate data:16,653, check:1
Calibrate data:17,676, check:1
Calibrate data:18,696, check:1
Calibrate data:19,717, check:1
Calibrate data:20,738, check:1
Calibrate data:21,756, check:1
Calibrate data:22,774, check:1
Calibrate data:23,792, check:1
Calibrate data:24,809, check:1
Calibrate data:25,824, check:1
Calibrate data:26,838, check:1
Calibrate data:27,853, check:1
Calibrate data:28,867, check:1
Calibrate data:29,879, check:1
Calibrate data:30,890, check:1
Calibrate data:31,901, check:1
Calibrate data:32,914, check:1
Calibrate data:33,924, check:1
Calibrate data:34,933, check:1
Calibrate data:35,942, check:1
Calibrate data:36,950, check:1
Calibrate data:37,1015, check:1
Calibrate data:38,1015, check:1
Calibrate data:39,1015, check:1

markniu, 2024-07-16:
how about increase the delay value `#define  I2C_BD_DELAY  20`  from 20 to 40  ?
and please use this firmware that I pulled to official marlin recently. https://github.com/markniu/MarlinPULL/tree/bugfix-2.1.x
https://github.com/MarlinFirmware/Marlin/pull/27243

peterstevey, 2024-07-16:
I have tried increasing the delay, but doesnt change it.

I will recompile with the bugfix code and see if that solves it. Thank you!

peterstevey, 2024-07-18:
Sorry - I have another issue now...

Homing works well, and z height is accurate!

When initiating G29, the axis are homed, but then marlin crashes and the printer restarts. Sometimes it beeps and just reports "error" on screen...

ABL is activated, probing for 16 points along x and y axis. BD_SENSOR_PROBE_NO_STOP is not enabled, however when enabled it errors out in a similar way.

ABL worked fine with the BLtouch before, so I'm pretty sure the rest of the code is fine...

markniu, 2024-07-18:
which bugfix marlin do you use? you can try the version https://github.com/markniu/MarlinPULL/tree/bugfix-2.1.x
there is a bug with BD_SENSOR_PROBE_NO_STOP if the ABL speed is fast in the official marlin github.

peterstevey, 2024-07-18:
That is the version that I'm using... I've disabled BD_SENSOR_PROBE_NO_STOP and still am getting the same error

markniu, 2024-07-19:
what's the error message?
how about disable the EEPROM and SDsupport for lite the firmware?

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

Closed 2025-02-13.

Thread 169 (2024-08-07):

problem with M119

tjengbudi, 2024-08-07:
hello
i connected bd sensor to my skr 1.4
i using bltouch port from the board. but cause the probing is cannot works i connect it to exp1 port. for sure i connect it to port p1.27

the schematic is right here
https://user-images.githubusercontent.com/74151066/98479426-84961880-21f7-11eb-8f3c-1270e7dc9f71.png

my settimg is

[BDsensor]
sda_pin: P1.27
scl_pin: P2.0
delay: 20
z_offset:0
x_offset: 0
y_offset: 34
position_endstop: 0.5
value is 0.5~1.0
collision_homing:0
collision_calibrate:0

M119 always return z: open
when i added metal under the sensor the light is on. but the M119 still said z:Open

M102 s-1
BDsensorVer:V1.2c pandapi3d     ,switch_mode=1,collision_homing=0,collision_cal=0

m102 s-2
3.01mm

i checked cable with multitester it is not broken at all

installed newest bdsensor script and klipper last version.

so i do not understand why this happened

markniu, 2024-08-08:
did you calibrate the BDsensor? you can calibrate the sensor again.

tjengbudi, 2024-08-08:
> did you calibrate the BDsensor? you can calibrate the sensor again.

already calibrate, calling m102 s-5 lowest value is 55

calibrate again after you asked and after calibrate m102 s-5 lowest value is 53

and it is still not triggered the z endstop.

tjengbudi, 2024-08-08:
i trying to change sda pin with random pin in the board but i not connect it to bd sensor. i want to make sure that i might have wrong connection. or cable error.

after restart, command m102 s-1 replied "No data or corrupt data from BDsensor(                    ), Please check connection"
so i am sure that i have connect it in the right pin and working

change it back and it replied "BDsensorVer:V1.2c pandapi3d     ,switch_mode=1,collision_homing=0,collision_cal=0"

must i flash it?

tjengbudi, 2024-08-08:
i use screw for the test looks like i do it wrong. test with wider dimension it triggered..

thankyou

Closed 2024-08-08.

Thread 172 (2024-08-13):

Sensor triggers in air

RealHaltewunsch, 2024-08-13:
I have the BDsensor M, I calibrated it and imI'm using these parameters: BDsensorVer:V1.2c,switch_mode=1,collision_homing=1,collision_cal=1

My config includes
[force_move]
enable_force_move: true

Still, every other time I try to print my probe triggers in air. The nozzle has a distance of about 3-5mm, the probe still has about 4-6mm distance to the bed.
Sometimes it triggers the first time correctly, but then on the second try it triggers in air and keeps going up and up and up.
I noticed that when the bed is heating I have a 0% chance of homing, so now I turn the heaters off before probing the bed, but still every other time it triggers in air and never finishes homing.

Klipper gives me following error:
warning: triggered in air, 743
BDsensorVer:V1.2c,switch_mode=1,collision_homing=1,collision_cal=1

My calibration reading is:
`17:10
805 at 3.9mm
17:10
797 at 3.8mm
17:10
783 at 3.7mm
17:10
783 at 3.6mm
17:10
776 at 3.5mm
17:10
767 at 3.4mm
17:10
758 at 3.3mm
17:10
751 at 3.2mm
17:10
742 at 3.1mm
17:10
731 at 3.0mm
17:10
720 at 2.9mm
17:10
710 at 2.8mm
17:10
697 at 2.7mm
17:10
685 at 2.6mm
17:10
673 at 2.5mm
17:10
658 at 2.4mm
17:10
643 at 2.3mm
17:10
631 at 2.2mm
17:10
616 at 2.1mm
17:10
601 at 2.0mm
17:10
581 at 1.9mm
17:10
544 at 1.8mm
17:10
545 at 1.7mm
17:10
526 at 1.6mm
17:10
503 at 1.5mm
17:10
487 at 1.4mm
17:10
462 at 1.3mm
17:10
439 at 1.2mm
17:10
416 at 1.1mm
17:10
395 at 1.0mm
17:10
372 at 0.9mm
17:10
343 at 0.8mm
17:10
319 at 0.7mm
17:10
294 at 0.6mm
17:10
267 at 0.5mm
17:10
246 at 0.4mm
17:10
222 at 0.3mm
17:10
199 at 0.2mm
17:10
174 at 0.1mm
17:10
153 at 0.0mm`

What can I do about it?

[config-20240813-171339.zip](https://github.com/user-attachments/files/16601625/config-20240813-171339.zip)
[klippy.log](https://github.com/user-attachments/files/16601626/klippy.log)

markniu, 2024-08-14:
seems need to increase the second homing speed.  set the `second_homing_speed `from 3 to 4 or 5

HelmutPirker, 2024-09-01:
Bei mir ist das jetzt auch der Fehler **warning: triggered in air ** angezeigt,. eine Erhörung  der zweiten Homing- Geschwindigkeit behebt den Fehler nicht. Was jetzt?

RealHaltewunsch, 2024-09-11:
@markniu thanks for your help, this solved it for me, I have set it to 4 and it homes fine every time.

Clarkbf, 2024-12-09:
I am having the same issue. When it fails though my bed slowly moves down (coreXY) until it crashes the bed into the bottom of the printer. The printer never stops the homing cycle unless I emergency stop the print.
my Z klipper stepper settings:

homing_speed: 6.0 # Leadscrews are slower than 2.4, 10 is a recommended max.
second_homing_speed: 5
homing_retract_dist: 6
homing_retract_speed: 10

markniu, 2024-12-10:
you can test with the slow speed at first ,
like `homing_speed: 4.0` and `second_homing_speed: 3`  also setting the `delay:10` value in `BDsensor `section

> I am having the same issue. When it fails though my bed slowly moves down (coreXY) until it crashes the bed into the bottom of the printer. The printer never stops the homing cycle unless I emergency stop the print. my Z klipper stepper settings:
>
> homing_speed: 6.0 # Leadscrews are slower than 2.4, 10 is a recommended max. second_homing_speed: 5 homing_retract_dist: 6 homing_retract_speed: 10

Clarkbf, 2024-12-10:
I have the delay value already at 10. Can this be a larger number? Wondering if retract distance should be adjusted as well? set to 6 right now.

markniu, 2024-12-10:
The delay value affects the communication speed of MCU with BDsensor. The larger the value, the slower the communication speed.
that retract_distance:6 is ok.

Clarkbf, 2024-12-10:
Why does the bed continue to move away from the bdsensor when it has the triggered in air issue and is there a way to stop it?

Closed 2024-09-11.

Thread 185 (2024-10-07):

No data or corrupt data from BDsensor(                    ), Please check connection

MDegelmann, 2024-10-07:
Hello, I can't get a connection
I use the Manta M8P and since the pins

sda_pin: PC9
scl_pin: PA8

Firmware is flashed and the version is: v0.12.0-316-g96cceed23-dirty

the sensor is v1.3

don't know what to do next

markniu, 2024-10-08:
how about use the probe pins:
sda_pin: PD13
scl_pin: PD12

MDegelmann, 2024-10-08:
The same problem No data or corrupt data from BDsensor( ), Please check connection

markniu, 2024-10-08:
does the light on while put a metal close the coil?  check again the 5v and other wire order.

MDegelmann, 2024-10-08:
111 / 5.000
Yes, the LED lights up when you hold a piece of metal to it.

I have checked all connections
GND
5V
SCL
GND
SDA

markniu, 2024-10-08:
What does the cable that comes with the BDsensor look like?

MDegelmann, 2024-10-08:
I measured the cable and everything has contact

markniu, 2024-10-08:
it can not be measured by multimeter sometimes.  what's the delay value in the BDsensor section? you can try to increase that value.

MDegelmann, 2024-10-08:
I was able to solve the problem.

I flashed the sensor and now it works

ceb0610, 2024-10-18:
Having the same problem but not having any luck flashing my sensor.

markniu, 2024-10-19:
> Having the same problem but not having any luck flashing my sensor.

which board and pins are used for the sensor?

ceb0610, 2024-10-19:
> > Having the same problem but not having any luck flashing my sensor.
>
> which board and pins are used for the sensor?

BD Sensor V1.3
ST-Link V2 connected according to the wiki. I have checked the wiring multiple times.

markniu, 2024-10-19:
sorry, I mean which the pins are used for the sensor on the mainboard of the printer?

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

ceb0610, 2024-10-19:
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

Using the BLTouch interface on my toolhead board. Getting 5V from another connector.

[BDsensor]
sda_pin:extra_mcu:PB6
scl_pin:extra_mcu:PB7

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

markniu, 2024-10-19:
do you have the electronic schematic ? you can check if there is a capacitor on the PB6 on the board

ceb0610, 2024-10-19:
> do you have the electronic schematic ? you can check if there is a capacitor on the PB6 on the board

No capacitor.

MDegelmann, 2024-11-07:
Problem durch neues flashen der Hardware gelöst

Closed 2024-11-07.

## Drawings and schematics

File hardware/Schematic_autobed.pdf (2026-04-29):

## CLK

## SDA

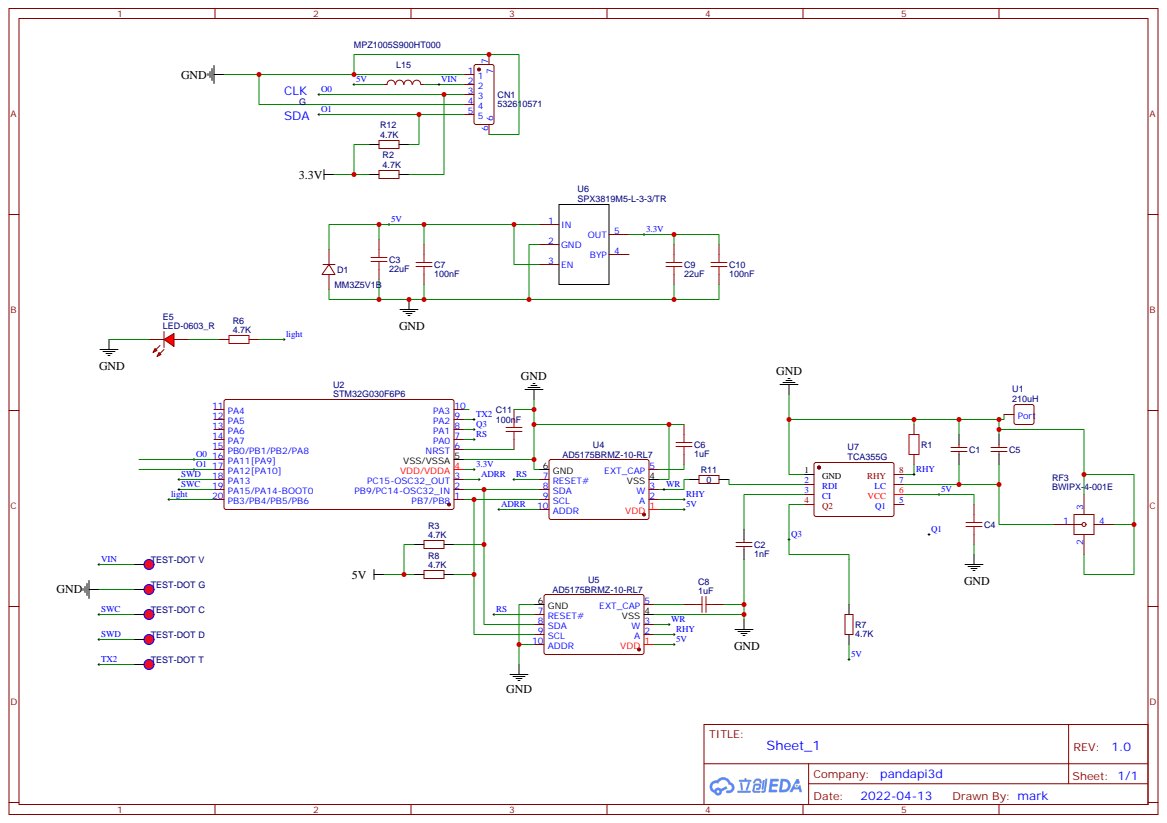
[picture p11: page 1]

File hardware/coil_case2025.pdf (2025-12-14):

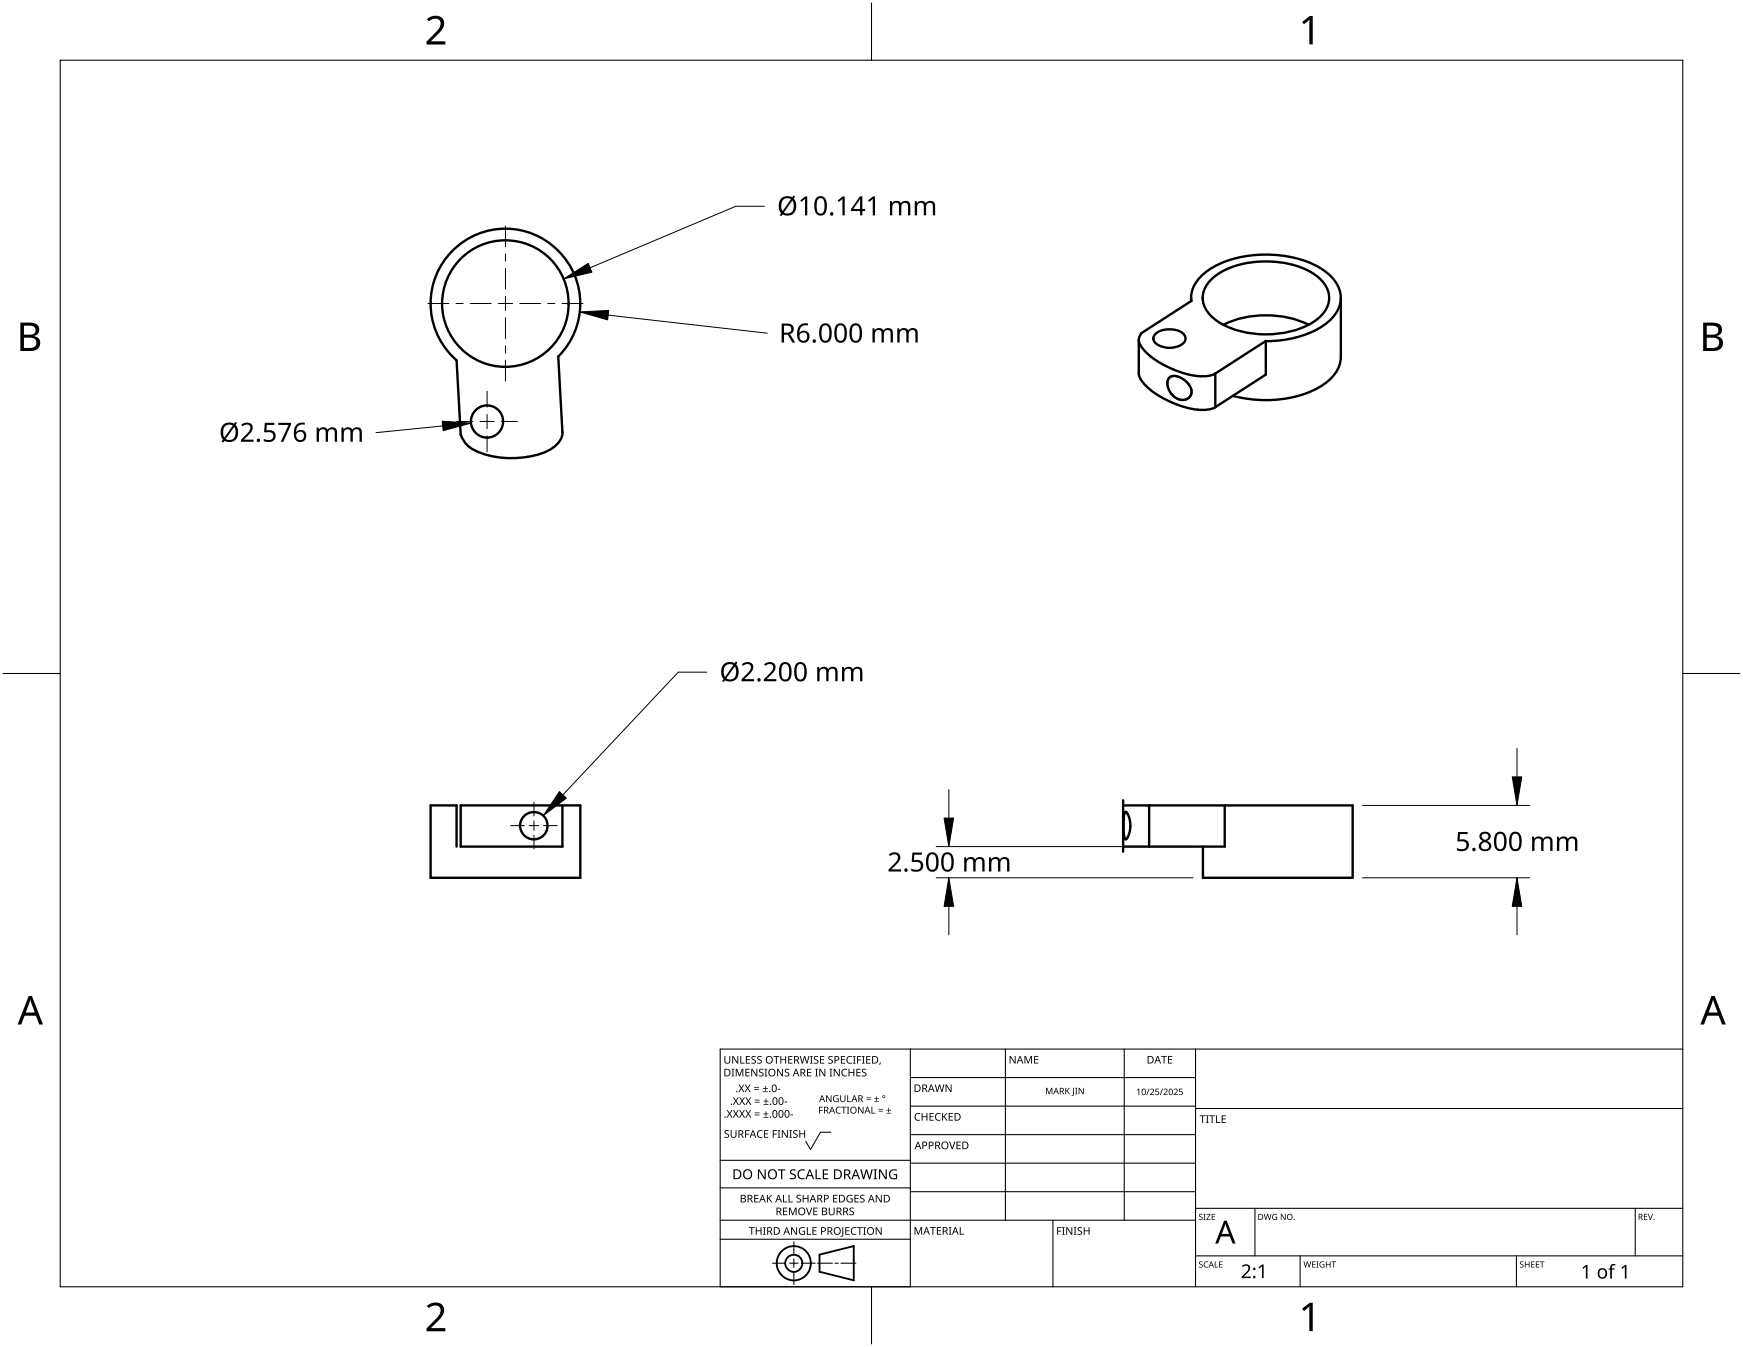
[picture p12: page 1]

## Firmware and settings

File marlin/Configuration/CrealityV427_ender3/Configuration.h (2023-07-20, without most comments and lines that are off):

#pragma once
#define BD_SENSOR_PROBE_NO_STOP
#define CONFIGURATION_H_VERSION 02010300
#define STRING_CONFIG_H_AUTHOR "(Dust, Ender-3)" // Who made the changes.
  #define MOTHERBOARD BOARD_CREALITY_V427
#define SERIAL_PORT 1
#define BAUDRATE 115200
#define CUSTOM_MACHINE_NAME "Ender-3 4.2.7"
#define X_DRIVER_TYPE  TMC2208_STANDALONE
#define Y_DRIVER_TYPE  TMC2208_STANDALONE
#define Z_DRIVER_TYPE  TMC2208_STANDALONE
#define E0_DRIVER_TYPE TMC2208_STANDALONE
#define EXTRUDERS 1
#define DEFAULT_NOMINAL_FILAMENT_DIA 1.75
#define TEMP_SENSOR_0 1
#define TEMP_SENSOR_1 0
#define TEMP_SENSOR_2 0
#define TEMP_SENSOR_3 0
#define TEMP_SENSOR_4 0
#define TEMP_SENSOR_5 0
#define TEMP_SENSOR_6 0
#define TEMP_SENSOR_7 0
#define TEMP_SENSOR_BED 1
#define TEMP_SENSOR_PROBE 0
#define TEMP_SENSOR_CHAMBER 0
#define TEMP_SENSOR_COOLER 0
#define TEMP_SENSOR_BOARD 0
#define TEMP_SENSOR_SOC 0
#define TEMP_SENSOR_REDUNDANT 0
#define DUMMY_THERMISTOR_998_VALUE  25
#define DUMMY_THERMISTOR_999_VALUE 100
#if TEMP_SENSOR_IS_MAX_TC(0)
  #define MAX31865_SENSOR_OHMS_0      100 // (Ω) Typically 100 or 1000 (PT100 or PT1000)
  #define MAX31865_CALIBRATION_OHMS_0 430 // (Ω) Typically 430 for Adafruit PT100; 4300 for Adafruit PT1000
#endif
#if TEMP_SENSOR_IS_MAX_TC(1)
  #define MAX31865_SENSOR_OHMS_1      100
  #define MAX31865_CALIBRATION_OHMS_1 430
#endif
#if TEMP_SENSOR_IS_MAX_TC(2)
  #define MAX31865_SENSOR_OHMS_2      100
  #define MAX31865_CALIBRATION_OHMS_2 430
#endif
#if HAS_E_TEMP_SENSOR
  #define TEMP_RESIDENCY_TIME         10  // (seconds) Time to wait for hotend to "settle" in M109
  #define TEMP_WINDOW                  1  // (°C) Temperature proximity for the "temperature reached" timer
  #define TEMP_HYSTERESIS              3  // (°C) Temperature proximity considered "close enough" to the target
#endif
#if TEMP_SENSOR_BED
  #define TEMP_BED_RESIDENCY_TIME     10  // (seconds) Time to wait for bed to "settle" in M190
  #define TEMP_BED_WINDOW              1  // (°C) Temperature proximity for the "temperature reached" timer
  #define TEMP_BED_HYSTERESIS          3  // (°C) Temperature proximity considered "close enough" to the target
#endif
#if TEMP_SENSOR_CHAMBER
  #define TEMP_CHAMBER_RESIDENCY_TIME 10  // (seconds) Time to wait for chamber to "settle" in M191
  #define TEMP_CHAMBER_WINDOW          1  // (°C) Temperature proximity for the "temperature reached" timer
  #define TEMP_CHAMBER_HYSTERESIS      3  // (°C) Temperature proximity considered "close enough" to the target
#endif
#if TEMP_SENSOR_REDUNDANT
  #define TEMP_SENSOR_REDUNDANT_SOURCE    E1  // The sensor that will provide the redundant reading.
  #define TEMP_SENSOR_REDUNDANT_TARGET    E0  // The sensor that we are providing a redundant reading for.
  #define TEMP_SENSOR_REDUNDANT_MAX_DIFF  10  // (°C) Temperature difference that will trigger a print abort.
#endif
#define HEATER_0_MINTEMP   5
#define HEATER_1_MINTEMP   5
#define HEATER_2_MINTEMP   5
#define HEATER_3_MINTEMP   5
#define HEATER_4_MINTEMP   5
#define HEATER_5_MINTEMP   5
#define HEATER_6_MINTEMP   5
#define HEATER_7_MINTEMP   5
#define BED_MINTEMP        5
#define CHAMBER_MINTEMP    5
#define HEATER_0_MAXTEMP 275
#define HEATER_1_MAXTEMP 275
#define HEATER_2_MAXTEMP 275
#define HEATER_3_MAXTEMP 275
#define HEATER_4_MAXTEMP 275
#define HEATER_5_MAXTEMP 275
#define HEATER_6_MAXTEMP 275
#define HEATER_7_MAXTEMP 275
#define BED_MAXTEMP      125
#define CHAMBER_MAXTEMP  60
#define HOTEND_OVERSHOOT 15   // (°C) Forbid temperatures over MAXTEMP - OVERSHOOT
#define BED_OVERSHOOT    10   // (°C) Forbid temperatures over MAXTEMP - OVERSHOOT
#define COOLER_OVERSHOOT  2   // (°C) Forbid temperatures closer than OVERSHOOT
#define PIDTEMP          // See the PID Tuning Guide at https://reprap.org/wiki/PID_Tuning
#define PID_MAX  255      // Limit hotend current while PID is active (see PID_FUNCTIONAL_RANGE below); 255=full current
#define PID_K1     0.95   // Smoothing factor within any PID loop
    #define DEFAULT_Kp  21.73
    #define DEFAULT_Ki   1.54
    #define DEFAULT_Kd  76.55
#define MAX_BED_POWER 255 // limits duty cycle to bed; 255=full current
#define MAX_CHAMBER_POWER 255 // limits duty cycle to chamber heater; 255=full current
  #define PID_FUNCTIONAL_RANGE 10 // If the temperature difference between the target temperature and the actual temperature
  #define PID_EDIT_MENU           // Add PID editing to the "Advanced Settings" menu. (~700 bytes of flash)
  #define PID_AUTOTUNE_MENU       // Add PID auto-tuning to the "Advanced Settings" menu. (~250 bytes of flash)
#define PREVENT_COLD_EXTRUSION
#define EXTRUDE_MINTEMP 170
#define PREVENT_LENGTHY_EXTRUDE
#define EXTRUDE_MAXLENGTH 200
#define THERMAL_PROTECTION_HOTENDS // Enable thermal protection for all extruders
#define THERMAL_PROTECTION_BED     // Enable thermal protection for the heated bed
#define THERMAL_PROTECTION_CHAMBER // Enable thermal protection for the heated chamber
#define THERMAL_PROTECTION_COOLER  // Enable thermal protection for the laser cooling
#define ENDSTOPPULLUPS
#define X_MIN_ENDSTOP_HIT_STATE HIGH
#define X_MAX_ENDSTOP_HIT_STATE HIGH
#define Y_MIN_ENDSTOP_HIT_STATE HIGH
#define Y_MAX_ENDSTOP_HIT_STATE HIGH
#define Z_MIN_ENDSTOP_HIT_STATE HIGH
#define Z_MAX_ENDSTOP_HIT_STATE HIGH
#define I_MIN_ENDSTOP_HIT_STATE HIGH
#define I_MAX_ENDSTOP_HIT_STATE HIGH
#define J_MIN_ENDSTOP_HIT_STATE HIGH
#define J_MAX_ENDSTOP_HIT_STATE HIGH
#define K_MIN_ENDSTOP_HIT_STATE HIGH
#define K_MAX_ENDSTOP_HIT_STATE HIGH
#define U_MIN_ENDSTOP_HIT_STATE HIGH
#define U_MAX_ENDSTOP_HIT_STATE HIGH
#define V_MIN_ENDSTOP_HIT_STATE HIGH
#define V_MAX_ENDSTOP_HIT_STATE HIGH
#define W_MIN_ENDSTOP_HIT_STATE HIGH
#define W_MAX_ENDSTOP_HIT_STATE HIGH
#define Z_MIN_PROBE_ENDSTOP_HIT_STATE HIGH
#define DEFAULT_AXIS_STEPS_PER_UNIT   { 80, 80, 400, 93 }
#define DEFAULT_MAX_FEEDRATE          { 500, 500, 5, 25 }
#define DEFAULT_MAX_ACCELERATION      { 500, 500, 100, 5000 }
#define DEFAULT_ACCELERATION                   500  // X, Y, Z ... and E acceleration for printing moves
#define DEFAULT_RETRACT_ACCELERATION           500  // E acceleration for retracts
#define DEFAULT_TRAVEL_ACCELERATION            500  // X, Y, Z ... acceleration for travel (non printing) moves
#define DEFAULT_EJERK    5.0  // May be used by Linear Advance
  #define JUNCTION_DEVIATION_MM 0.08  // (mm) Distance from real junction edge
  #define JD_HANDLE_SMALL_SEGMENTS    // Use curvature estimation instead of just the junction angle
#define USE_PROBE_FOR_Z_HOMING
#define NOZZLE_TO_PROBE_OFFSET { -34, 0, 0 }
#define PROBING_TOOL 0
#define PROBING_MARGIN 10
#define XY_PROBE_FEEDRATE (133*60)
#define Z_PROBE_FEEDRATE_FAST (4*60)
#define Z_PROBE_FEEDRATE_SLOW (Z_PROBE_FEEDRATE_FAST / 2)
#define Z_CLEARANCE_DEPLOY_PROBE   0 // Z Clearance for Deploy/Stow
#define Z_CLEARANCE_BETWEEN_PROBES  1 // Z Clearance between probe points
#define Z_CLEARANCE_MULTI_PROBE     1 // Z Clearance between multiple probes
#define Z_PROBE_LOW_POINT          -2 // Farthest distance below the trigger-point to go before stopping
#define Z_PROBE_OFFSET_RANGE_MIN -20
#define Z_PROBE_OFFSET_RANGE_MAX 20
#define X_ENABLE_ON 0
#define Y_ENABLE_ON 0
#define Z_ENABLE_ON 0
#define E_ENABLE_ON 0 // For all extruders
#define INVERT_X_DIR false
#define INVERT_Y_DIR false
#define INVERT_Z_DIR true
#define INVERT_E0_DIR false
#define INVERT_E1_DIR false
#define INVERT_E2_DIR false
#define INVERT_E3_DIR false
#define INVERT_E4_DIR false
#define INVERT_E5_DIR false
#define INVERT_E6_DIR false
#define INVERT_E7_DIR false
#define X_HOME_DIR -1
#define Y_HOME_DIR -1
#define Z_HOME_DIR -1
#define X_BED_SIZE 235
#define Y_BED_SIZE 235
#define X_MIN_POS 0
#define Y_MIN_POS 0
#define Z_MIN_POS 0
#define X_MAX_POS X_BED_SIZE
#define Y_MAX_POS Y_BED_SIZE
#define Z_MAX_POS 250
#define MIN_SOFTWARE_ENDSTOPS
  #define MIN_SOFTWARE_ENDSTOP_X
  #define MIN_SOFTWARE_ENDSTOP_Y
  #define MIN_SOFTWARE_ENDSTOP_Z
  #define MIN_SOFTWARE_ENDSTOP_I
  #define MIN_SOFTWARE_ENDSTOP_J
  #define MIN_SOFTWARE_ENDSTOP_K
  #define MIN_SOFTWARE_ENDSTOP_U
  #define MIN_SOFTWARE_ENDSTOP_V
  #define MIN_SOFTWARE_ENDSTOP_W
#define MAX_SOFTWARE_ENDSTOPS
  #define MAX_SOFTWARE_ENDSTOP_X
  #define MAX_SOFTWARE_ENDSTOP_Y
  #define MAX_SOFTWARE_ENDSTOP_Z
  #define MAX_SOFTWARE_ENDSTOP_I
  #define MAX_SOFTWARE_ENDSTOP_J
  #define MAX_SOFTWARE_ENDSTOP_K
  #define MAX_SOFTWARE_ENDSTOP_U
  #define MAX_SOFTWARE_ENDSTOP_V
  #define MAX_SOFTWARE_ENDSTOP_W
#define AUTO_BED_LEVELING_BILINEAR
#define BD_SENSOR
  #define ENABLE_LEVELING_FADE_HEIGHT
    #define DEFAULT_LEVELING_FADE_HEIGHT 10.0 // (mm) Default fade height.
  #define SEGMENT_LEVELED_MOVES
  #define LEVELED_SEGMENT_LENGTH 5.0 // (mm) Length of all segments (except the last one)
  #define GRID_MAX_POINTS_X 3
  #define GRID_MAX_POINTS_Y GRID_MAX_POINTS_X
#define Z_SAFE_HOMING
  #define Z_SAFE_HOMING_X_POINT X_CENTER  // X point for Z homing
  #define Z_SAFE_HOMING_Y_POINT Y_CENTER  // Y point for Z homing
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

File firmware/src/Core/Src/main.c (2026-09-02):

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
/* Includes ------------------------------------------------------------------*/
#include "main.h"
#include "i2c.h"
#include "usart.h"
#include "gpio.h"


/* USER CODE BEGIN PV */
#include "flash.h"
/* USER CODE END PV */

void SystemClock_Config(void);
/* USER CODE BEGIN PFP */
#define POINTS 75

int filter_s = 0, filter_n = 0, filter_s_old = 0;
unsigned char num = 0;
unsigned short table_point[POINTS];

/* LED behaviour:
 * 0: off    (disconnected & out of range)
 * 1: on     (disconnected & metal detected)
 * 2: flash  (connected & metal detected)
 * 3: blink  (connected & out of range) */
int led_status = 0;
int connected_flag = 0;            /* set once a host read completes */

/* Firmware version string, streamed to the host when reading address 1016 */
const unsigned char sensor_info[20] = {'V','1','.','2','d',' ','p','a','n','d','a','p','i','3','d','\n','\0'};

/* Busy-wait delay of ~nus, calibrated for the 64 MHz system clock */
void for_delay_us(uint32_t nus)
{
    uint32_t Delay = nus * 64 / 64;
    do
    {
        __NOP();
    }
    while (Delay--);
}

#define delay_ms   HAL_Delay

#define LED_ON  HAL_GPIO_WritePin(GPIOB, GPIO_PIN_3, GPIO_PIN_SET)
#define LED_OFF HAL_GPIO_WritePin(GPIOB, GPIO_PIN_3, GPIO_PIN_RESET)

/* Software 2-wire slave bus (ported from an 8051 design where CLK was the
 * INT0 pin P3.2 and SDA was the INT1 pin P3.3) */
#define CLK_I2C_R HAL_GPIO_ReadPin(GPIOA, GPIO_PIN_11)
#define SDA_I2C_R HAL_GPIO_ReadPin(GPIOA, GPIO_PIN_12)

int SDA_int_or_output = 0;         /* 0: PA12 is EXTI input, 1: PA12 is open-drain output */

/* Reconfigure PA12 (SDA) as edge-triggered interrupt input */
void SDA_AS_INT()
{
    GPIO_InitTypeDef GPIO_InitStruct = {0};

    GPIO_InitStruct.Pin  = GPIO_PIN_12;
    GPIO_InitStruct.Mode = GPIO_MODE_IT_RISING_FALLING;
    GPIO_InitStruct.Pull = GPIO_PULLUP;
    HAL_GPIO_Init(GPIOA, &GPIO_InitStruct);
    SDA_int_or_output = 0;
}

/* Reconfigure PA12 (SDA) as open-drain output */
void SDA_AS_output()
{
    GPIO_InitTypeDef GPIO_InitStruct = {0};

    GPIO_InitStruct.Pin   = GPIO_PIN_12;
    GPIO_InitStruct.Mode  = GPIO_MODE_OUTPUT_OD;
    GPIO_InitStruct.Pull  = GPIO_PULLUP;
    GPIO_InitStruct.Speed = GPIO_SPEED_FREQ_LOW;
    HAL_GPIO_Init(GPIOA, &GPIO_InitStruct);
    SDA_int_or_output = 1;
}

/* Drive the SDA line (switches PA12 to output first if needed) */
void SDA_I2C_W(int vl)
{
    if (SDA_int_or_output == 0)
        SDA_AS_output();
    HAL_GPIO_WritePin(GPIOA, GPIO_PIN_12, vl);
}

/* Comparator output of the oscillator circuit */
#define Q3_pin HAL_GPIO_ReadPin(GPIOA, GPIO_PIN_1)

/* Software emulations of the 8051 EX0/EX1 interrupt-enable bits:
 * EX0 gates the CLK edge interrupt, EX1 gates the SDA edge interrupt */
int EX0 = 0, EX1 = 0;

/* Slave state machine:
 * -2: switch mode (SDA driven as the probe output)
 * -1: idle
 *  0: start condition seen
 *  1: clock high, sampling the R/W bit
 *  2: reading (shifting the 11-bit data word out)
 *  3: writing (shifting the 11-bit address word in)
 *  4: writing data (bits counted only, payload unused)
 *  5: transfer finished */
int I2C_status = -1;
int switch_value = -1;             /* >= 0: switch mode active, holds the trigger threshold */

unsigned short data_addr = 0;      /* last address received from the master (10-bit payload) */
unsigned short data_i = 0;         /* bit counter of the word being shifted */
unsigned short on_data = 0, off_data = 0, on_send_data = 0;
unsigned int i2c_timeout = 0;
unsigned short data_send = 0;

/* Readout selector, also used as a streaming counter:
 * 0:                calibrated distance in 0.1 mm units
 * 1:                raw oscillator value
 * 2 .. POINTS+1:    calibration table entries
 * POINTS+2 .. +21:  version string characters */
unsigned char read_raw = 0;

char tmp_d, need_flash = 0;        /* need_flash: 1 clear table, 2/3 erase+save to flash, 4 reboot */
char flash_flag = 0;
unsigned int i2c_timeout_j = 0;

/* Append an even-parity bit (bit 10) to a 10-bit value */
unsigned short Add_OddEven(unsigned short byte)
{
    unsigned char i;
    unsigned char n;               /* count of set bits */
    unsigned short r;              /* result */

    n = 0;
    for (i = 0; i < 10; i++)
    {
        if (((byte >> i) & 0x01) == 0x01)
        {
            n++;
        }
    }
    if ((n & 0x01) == 0x01)
    {
        r = byte | 0x400;          /* odd count of ones: set the parity bit */
    }
    else
    {
        r = byte | 0x00;           /* even count of ones: leave the parity bit clear */
    }
    return r;
}

#define BYTE_CHECK_OK     0x01
#define BYTE_CHECK_ERR    0x00

/* Verify the even-parity bit (bit 10) of an 11-bit word.
 * Returns BYTE_CHECK_OK when the parity matches, BYTE_CHECK_ERR otherwise. */
unsigned short Check_OddEven(unsigned short byte)
{
    unsigned char i;
    unsigned char n;               /* count of set bits */
    unsigned char r;               /* result */

    n = 0;
    for (i = 0; i < 10; i++)
    {
        if (((byte >> i) & 0x01) == 0x01)
        {
            n++;
        }
    }
    if ((byte >> 10) == (n & 0x01))   /* parity bit must equal the count of ones */
    {
        r = BYTE_CHECK_OK;
    }
    else
    {
        r = BYTE_CHECK_ERR;
    }
    return r;
}

/* Convert a raw oscillator value to a distance using the calibration table.
 * Pass 1 (always): find the nearest calibrated entry (skips 0xffff entries).
 * Pass 2 (Tdata == 1): linear interpolation between neighbouring entries,
 * giving the distance in 0.1 mm units, clamped to 1022. */
unsigned short cover_to_distance(unsigned short raw_data, unsigned char Tdata)
{
    unsigned short d_i, d_j, d_x, i;

    d_j = 0;
    d_x = 0;
    d_i = 0xffff;
    for (i = 0; i < POINTS; i++)
    {
        if (table_point[i] != 0xffff)
        {
            if (raw_data > table_point[i])
                d_j = raw_data - table_point[i];
            else
                d_j = table_point[i] - raw_data;
            if (d_i > d_j)         /* keep the closest match seen so far */
            {
                d_i = d_j;
                d_x = i;
            }
        }
    }
    if (Tdata == 1)
    {
        if (raw_data > table_point[d_x])
        {
            /* interpolate towards the next entry */
            d_i = (raw_data - table_point[d_x]) * 10;
            d_j = ((table_point[d_x + 1] - table_point[d_x]) * 10 / 10);
            if (d_j > 0)
                d_x = d_x * 10 + d_i / d_j;
            else
                d_x = d_x * 10;
        }
        else
        {
            if (d_x >= 1)
            {
                /* interpolate towards the previous entry */
                d_i = (table_point[d_x] - raw_data) * 10;
                d_j = ((table_point[d_x] - table_point[d_x - 1]) * 10 / 10);
                if (d_j > 0)
                    d_x = d_x * 10 - d_i / d_j;
                else
                    d_x = d_x * 10;
            }
        }
    }

    if (d_x > 1023)
        d_x = 1022;
    return d_x;
}

#include <stdio.h>
#define I2C_ADDRESS 0x2F          /* 7-bit address of the excitation chip on hardware I2C1 */
int extt = 0;                     /* last EXTI edge seen, debug aid */

#define COUNTOF(__BUFFER__)   (sizeof(__BUFFER__) / sizeof(*(__BUFFER__)))
#define TXBUFFERSIZE          (COUNTOF(aTxBuffer) - 1)
/* Size of reception buffer */
#define RXBUFFERSIZE          TXBUFFERSIZE

/* CLK edge interrupt handler: runs the software 2-wire slave state machine */
void clk_int_callback(void)
{
    i2c_timeout++;
    switch (I2C_status)
    {
        case -2:                  /* switch mode: a CLK level change exits it */
            if (CLK_I2C_R == 1)
            {
                I2C_status = -1;
                i2c_timeout = 0;
                switch_value = -1;
                EX0 = 0;
                EX1 = 1;
                SDA_AS_INT();
            }
            break;

        case 0:                   /* start seen: wait for CLK low and SDA low */
            if (CLK_I2C_R == 0 && SDA_I2C_R == 0)
            {
                I2C_status = 1;
                i2c_timeout_j = 0;
            }
            else
            {
                i2c_timeout++;
            }
            break;

        case 1:                   /* first clock high: sample the R/W bit */
            if (CLK_I2C_R == 1)
            {
                if (SDA_I2C_R)
                {
                    I2C_status = 2;               /* read */
                    /* select the word to shift out */
                    if (read_raw == 0)
                        data_send = Add_OddEven(on_send_data);
                    else if (read_raw == 1)
                        data_send = Add_OddEven(on_data);
                    else if (read_raw >= 2 && read_raw < (POINTS + 2))
                    {
                        data_send = table_point[read_raw - 2];
                        data_send = Add_OddEven(data_send);
                        read_raw++;
                    }
                    else if (read_raw >= (POINTS + 2) && read_raw < (POINTS + 2 + 20))
                    {
                        data_send = sensor_info[read_raw - 2 - POINTS];
                        data_send = Add_OddEven(data_send);
                        read_raw++;
                    }
                }
                else
                {
                    I2C_status = 3;               /* write */
                    data_addr = 0;
                }
                data_i = 0;
            }
            break;

        case 2:                   /* read: shift data_send out MSB first on CLK low */
            if (CLK_I2C_R == 0)
            {
                if (data_i > 10)
                {
                    data_i = 0;
                    i2c_timeout = 0;
                    I2C_status = 5;
                    connected_flag = 1;
                    break;
                }
                SDA_I2C_W(((data_send >> (10 - data_i)) & 0x01));
                data_i++;
            }
            break;

        case 3:                   /* write: shift the address in MSB first on CLK high */
            if (CLK_I2C_R == 1)
            {
                if (SDA_I2C_R)
                    data_addr = (data_addr | (1 << (10 - data_i)));
                data_i++;
                if (data_i > 10)
                {
                    data_i = 0;
                    I2C_status = 5;
                    EX0 = 0;      /* disable CLK edges */
                    EX1 = 1;      /* enable SDA edges, wait for the stop condition */
                    SDA_AS_INT();
                    if (Check_OddEven(data_addr) == BYTE_CHECK_ERR)
                        break;
                    data_addr = (data_addr & 0x3ff);
                    if (switch_value >= 0 && data_addr < 900)
                    {
                        /* update the probe trigger threshold */
                        switch_value = data_addr;
                        I2C_status = -3;
                        break;
                    }
                    if (data_addr < POINTS)
                    {
                        /* calibration: store the current raw value for this point */
                        table_point[data_addr] = on_data;
                    }
                    else if (data_addr == 1020)          /* read raw data */
                    {
                        read_raw = 1;
                    }
                    else if (data_addr == 1019)          /* start calibration */
                    {
                        need_flash = 1;
                    }
                    else if (data_addr == 1016)          /* read version data */
                    {
                        read_raw = POINTS + 2;
                    }
                    else if (data_addr == 1021)          /* finish calibration: erase and save to flash */
                    {
                        need_flash = 2;
                    }
                    else if (data_addr == 1017)          /* read calibration data */
                    {
                        read_raw = 2;
                    }
                    else if (data_addr == 1018)          /* end reading calibration/version data */
                    {
                        read_raw = 0;
                    }
                    else if (data_addr == 1022)          /* reboot */
                    {
                        need_flash = 4;
                    }
                    else if (data_addr == 1023)          /* enter switch mode: send 1023, send the trigger
                                                           value, then SDA becomes the probe output; a CLK
                                                           level change exits switch mode */
                    {
                        switch_value = 0;
                    }
                }
            }
            break;

        case 4:                   /* write data: count the bits, payload unused */
            if (CLK_I2C_R == 0)
            {
                data_i++;
                if (data_i > 9)
                {
                    data_i = 0;
                    I2C_status = 5;
                }
            }
            break;

        case 5:                   /* transfer finished: arm stop detection */
            EX0 = 0;
            EX1 = 1;
            SDA_AS_INT();
            break;

        default:
            break;
    }
}

/* SDA edge interrupt handler: start/stop condition detection */
void sda_int_callback()
{
    EX0 = 0;

    switch (I2C_status)
    {
        case 0:
        case -1:
            if ((SDA_I2C_R == 0) && CLK_I2C_R)      /* start condition */
            {
                I2C_status = 0;
                data_i = 0;
                EX1 = 0;          /* disable SDA edges */
                EX0 = 1;          /* enable CLK edges */
            }
            break;

        case 2:
        case 4:
        case 5:
            break;

        default:
            break;
    }

    if ((SDA_I2C_R == 1) && CLK_I2C_R)              /* stop condition */
    {
        if (I2C_status == -3)     /* switch-mode threshold just written */
        {
            EX0 = 1;
            EX1 = 0;
            SDA_AS_output();
            i2c_timeout = 0;
            I2C_status = -2;
            return;
        }
        else
            I2C_status = -1;
        EX0 = 0;
        EX1 = 1;
        SDA_AS_INT();
        i2c_timeout = 0;
    }
}

void HAL_GPIO_EXTI_Rising_Callback(uint16_t GPIO_Pin)
{
    if (GPIO_Pin == GPIO_PIN_11)
    {
        extt = 1;
        if (EX0)
            clk_int_callback();
    }
    else if (GPIO_Pin == GPIO_PIN_12)
    {
        extt = 3;
        if (EX1)
            sda_int_callback();
    }
}

void HAL_GPIO_EXTI_Falling_Callback(uint16_t GPIO_Pin)
{
    if (GPIO_Pin == GPIO_PIN_11)
    {
        extt = 2;
        if (EX0)
            clk_int_callback();
    }
    else if (GPIO_Pin == GPIO_PIN_12)
    {
        extt = 4;
        if (EX1)
            sda_int_callback();
    }
}

/* Write one command word to the excitation chip on hardware I2C1.
 * The 2-byte frame packs the 6-bit command and the upper bits of DAT. */
char I2C_TransmitData(uint16_t i2c_address, unsigned char command, unsigned short DAT)
{
    uint8_t txbuf[3];

    command = (command << 2) | (DAT >> 8);
    i2c_address = i2c_address << 1;
    txbuf[0] = command;
    txbuf[1] = DAT & 0xff;

    if (HAL_I2C_Master_Transmit(&hi2c1, (uint16_t)i2c_address, (uint8_t *)txbuf, 2, 1000) != HAL_OK)
    {
        USART2_printf(" i2c error2\r\n");
        if (HAL_I2C_GetError(&hi2c1) != HAL_I2C_ERROR_AF)
        {
            USART2_printf(" i2c error\r\n");
            return 1;
        }
    }
    return (0);
}

/* USER CODE END PFP */

/* USER CODE BEGIN 0 */
uint8_t aTxBuffer[] = " test  ";   /* test buffer referenced by the TXBUFFERSIZE macro */

/* USER CODE BEGIN 0 */
/* Bus watchdog: reset the slave state machine when a transfer stalls
 * mid-frame, and execute the reboot request (need_flash == 4). */
void time_out_process()
{
    if (I2C_status >= 0)
        i2c_timeout++;
    else
        i2c_timeout = 0;

    if (I2C_status == -1)
        i2c_timeout_j++;
    else
        i2c_timeout_j = 0;

    if ((i2c_timeout > 5000 && I2C_status != -2) || need_flash == 4)   /* 5000 calls is about 1 s */
    {
        need_flash = 0;
        i2c_timeout = 0;
        I2C_status = -1;
        EX0 = 0;
        EX1 = 1;
        SDA_AS_INT();
        NVIC_SystemReset();
    }
}

#define T_HOLD    220            /* legacy tuning constant, currently unused */

void init_T1(void)
{
}
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
int main(void)
{
  /* USER CODE BEGIN 1 */
    int i = 0;
    int rdata = 0, of_data = 0;
    int old_on_data, old_of_data;
    int j = 0;
    int ret = 0;
    switch_value = -1;

  /* USER CODE END 1 */

  /* MCU Configuration--------------------------------------------------------*/

  /* Reset of all peripherals, Initializes the Flash interface and the Systick. */
  HAL_Init();

  /* Configure the system clock */
  SystemClock_Config();

  /* Initialize all configured peripherals */
  MX_GPIO_Init();
  MX_I2C1_Init();
  MX_USART2_UART_Init();
  /* USER CODE BEGIN 2 */
    LED_ON;

    /* reset the excitation/AD chip */
    HAL_GPIO_WritePin(GPIOA, GPIO_PIN_0, GPIO_PIN_RESET);
    HAL_Delay(100);
    HAL_GPIO_WritePin(GPIOA, GPIO_PIN_0, GPIO_PIN_SET);
    HAL_Delay(100);

    delay_ms(100);

    /* load the calibration table from the last flash page */
    for (i = 0; i < POINTS; i++)
    {
        table_point[i] = STMFLASH_ReadByte(STM32_FLASH_BASE + i * 2 + 1) << 8 | STMFLASH_ReadByte(STM32_FLASH_BASE + i * 2);
        USART2_printf("%d:%u; ", i, table_point[i]);
    }

    USART2_printf((char *)sensor_info);
    rdata = T_MIN;
    on_send_data = on_data = 0;   /*1010*/
    HAL_GPIO_WritePin(GPIOC, GPIO_PIN_15, GPIO_PIN_RESET);
    EX0 = 0;
    EX1 = 1;
    LED_OFF;

    /* initial excitation chip setup */
    I2C_TransmitData(0x2f, 0x07, 0x02);
    I2C_TransmitData(addr2, 0x07, 0x02);

    /* Main loop: triangular sweep of the excitation value. The comparator
     * (Q3_pin) flips when the oscillator starts/stops, and the sweep value
     * at that edge is the raw reading for the current distance. */
    while (1)
    {
        /* background commands processing */
        command_process();

        /* oscillator still running: no target in range, sweep up */
        while (Q3_pin == C_ON)
        {
            command_process();
            ret = I2C_TransmitData(0x2f, 1, rdata);
            if (ret > 0)
                USART2_printf("err0:%d,", ret);
            rdata += j;
            if (rdata <= T_MIN)
            {
                j = Del;
                rdata = T_MIN;
            }
            else if (rdata >= T_MAX)
            {
                j = -Del;
                rdata = T_MAX;
            }
            /* poll for the comparator to trip */
            i = 0;
            while (i < 10)
            {
                for_delay_us(100);
                if (Q3_pin == C_OFF)
                {
                    for_delay_us(1000);
                    break;
                }
                i++;
            }
            if (Q3_pin == C_OFF)
            {
                out_range_count = 0;
                on_data = rdata;   /* captured raw value at the trip point */
                j = Del;
                break;
            }
        }

        /* oscillator stopped: target detected, sweep down until it restarts */
        while (Q3_pin == C_OFF)
        {
            command_process();
            ret = I2C_TransmitData(0x2f, 1, rdata);
            if (ret > 0)
                USART2_printf("err1:%d,", ret);
            rdata += j;
            if (rdata <= T_MIN)
            {
                j = Del;
                rdata = T_MIN;
            }
            else if (rdata >= T_MAX)
            {
                j = -Del;
                rdata = T_MAX;
            }
            i = 0;
            while (i < 10)
            {
                for_delay_us(100);
                if (Q3_pin == C_ON) break;
                i++;
            }
            if (Q3_pin == C_ON)
            {
                out_range_count = 0;
                of_data = rdata;

                /* switch mode 1: filtered press detection on SDA */
                if (I2C_status == -2 && switch_value == 1)
                {
                    filter_s += on_data;
                    filter_n++;
                    if (filter_n >= 1)
                    {
                        filter_n = 0;
                        /* stable within +/-4 counts and in range: press */
                        if ((abs_i(filter_s, filter_s_old) < 4) && on_data < 750)
                        {
                            SDA_I2C_W(1);
                            USART2_printf(" press %d,%d,%d\n", on_data, filter_s, filter_s_old);
                        }
                        else
                        {
                            SDA_I2C_W(0);
                        }
                        if (filter_s != filter_s_old)
                            filter_s_old = filter_s;
                        filter_s = 0;
                    }
                }

                /* new reading: convert and report */
                if (old_on_data != on_data || old_of_data != of_data)
                {
                    old_on_data = on_data;
                    old_of_data = of_data;
                    on_send_data = cover_to_distance(on_data, 1);
                    USART2_printf("%d,%d\n", on_data, I2C_status);
                }
                j = -Del;
                break;
            }
        }
    }


  /* USER CODE END 2 */

  /* Infinite loop */
  /* USER CODE BEGIN WHILE */
  while (1)
  {
    /* USER CODE END WHILE */

    /* USER CODE BEGIN 3 */
  }
  /* USER CODE END 3 */
}

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


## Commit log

2022-05-18 add bed distance sensor test code and marlin code
    [Configuration.h, Configuration_adv.h, esp32.csv]
2022-05-19 Read z min enstop state from the BDsensor I2C
    [Configuration.h]
2022-05-21 use I2C library ; add new function for G102
    G102 T-1 Read raw Calibrate data
    G102 T-2 Start Calibrate
    G102 T4 Set the adjustable max Z hight is 0.4mm, if value==0,disable adjust z hight.
2022-05-22 fix some printing test problem
    [Configuration.h, Configuration_adv.h]
2022-05-25 add protection for bd sensor be moved out of the bed area.
2022-05-27 move bd sensor process code to idle loop
2022-05-29 fix printing bug
2022-05-30 update new shell
    [rounddown.stl, roundup.stl]
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2022-06-27 update test code
    [coil0.stl, coil_cover.stl, rounddown.stl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]
2022-06-29 the source code for marlin is moved to other github,see the readme
    [Configuration.h, Configuration_adv.h, esp32.csv]
2022-07-08 update to Marlin2.1
    [Configuration.h, Configuration_adv.h, esp32.csv]
2022-07-16 support mesh bed level with BD sensor
    [Configuration.h]
2022-07-20 support printerer20
    [Configuration_adv.h, Configuration_er20.h]
2022-07-28 a simple firmware flash tool for avr arduino printer
2022-09-07 update the images files
    [coil0.stl, coil_cover.stl]
2022-09-07 update coil sensor case
    [Coil_case.stl, coil0.stl, coil_cover.stl]
2022-09-09 the official marlin have been integrated this sensor
    [Configuration.h, Configuration_adv.h, Configuration_er20.h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]
2023-01-12 Support Klipper
    [bed_screws.cfg, bltouch.cfg, calibrate_size.scad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]
2023-01-12 remove klipper to other github
    [bed_screws.cfg, bltouch.cfg, calibrate_size.scad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]
2023-03-15 add config for klipper
    [generic-bigtreetech-octopus.cfg]
2023-03-16 Rename the folder name
    [generic-bigtreetech-octopus.cfg]
2023-05-01 update size
    [Coil_size.stl]
2023-05-10 install BDsensor into Klippere
    [generic-bigtreetech-octopus.cfg]
2023-05-10 fix a fast probe of klipper bug
    [BD_sensor.c]
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2023-05-18 fast probe bug: the max x axis point should - x_offset
    [BDsensor.py]
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2023-05-20 fix a bug of fast probe while the dir pin is invert
    [BD_sensor.c, BDsensor.py]
2023-05-21 fix the function of delay not accurate
    fix the function of delay not accurate . and set the default delay value to 20 that means 20us
    [BD_sensor.c, BDsensor.py]
2023-05-21 fix a fast probe bug
    [BD_sensor.c, BDsensor.py]
2023-05-23 optimize, set the mcu timer period from python
2023-05-26 support connect BDsensor on CAN bus extruder board
    support connect BDsensor on CAN bus extruder board
    add calibrate status message on the webpage
2023-05-29 support connect BDsensor to can bus board
    support connect BDsensor to can bus board without no_stop_probe
2023-05-30 change reading sensor period time: 100ms for idle, 5ms for homing z
2023-06-01 New Fast probe without move stop
    New fast probe (estimate time) without move stop
2023-06-02 set no_stop_probe only works for bed mesh calibarte command
2023-06-05 fix a bug for back to other probe, and it can not do mesh probe
2023-06-08 add protection while probe or homing; add position_endstop for no need to homing at zero z axis
2023-06-10 optimzite the code and add error stop while homing and probe
    [BD_sensor.c, BDsensor.py]
2023-06-15 clear some code; add 4ms delay before probe
2023-06-16 Disable toolhead rise up/down while probe with BDsensor
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2023-06-17 move the stl file into root folder
    [Coil_size.stl]
2023-06-19 add mount distance check while read calibrate data
2023-06-25 add user message of mount distance checking too high or too low
    [BDsensor.py]
2023-07-01 no need to slow down the second home speed for high homing accuracy
    [Coil_case.stl]
2023-07-01 allow z axis up and down while doing z_tilt probe as normal proximity sensor
    allow z axis up and down while doing z_tilt probe , so no limited of horizontal_move_z in [z_tilt], but slow down the speed of probe, E.g. adding speed:0.5 in the [BDsensor]
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2023-07-06 update the model of sensor
    [Coi_casel.stl, Coil_case.stl, PCB_case.stl]
2023-07-12 Move probe code into BDsensor.py, so now there is no python code is changed of stock Klipper
2023-07-15 add second pass for bed mesh in fast probe mode of no_stop_probe
2023-07-18 support second mesh bed pass while in no_stop_probe
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2023-07-20 add example configuration for Creality boardV4.2.7 ender3
    [Configuration.h, Configuration_adv.h]
2023-07-25 allow z_offset to be used as z axis adjust
2023-07-29 clear code: no patch code needed into endstop.c of klipper
2023-07-29 clear code: remove patch code in probe.py of klipper
2023-08-01 code clean up: no need to change klipper source code
    code clean up: no need to change klipper source code
    just add BDsensor.py and BD_sensor.c
2023-08-09 no need to slow down probe speed while doing z tilt
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2023-09-11 clear up code for "too many ids message error"
    [BD_sensor.c, BDsensor.py]
2023-09-14 examle config for delta printer
    [printer.cfg]
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2023-11-01 disable z move while doing probe accuracy check; add real time test
2023-11-21 add real time leveling
    [coil_case17.stl]
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2023-12-05 add support z endstop pin working with bdsensor
2023-12-12 invert z_adjust direction as z_offset；add new command，
    1, add new command:
    BDSENSOR_VERSION //replace M102 S-1
    BDSENSOR_CALIBRATE //replace M102 S6
    BDSENSOR_READ_CALIBRATION //replace M102 S-5
    BDSENSOR_DISTANCE //replace M102 S-2
    BDSENSOR_SET // set value, now only for setting z_adjust, for example BDSENSOR_SET z_adjust=0.1
    2, invert z_adjust direction as z_offset
    3,support z endstop pin working with bdsensor
    4,use G1 move for calibration
    [BD_sensor.c, BDsensor.py]
2023-12-13 fix the bug caused by the new feature
    [BDsensor.py]
2023-12-16 fix using the extra endstop pin bug
    [BDsensor.py]
2023-12-23 report more data instead of shutdown while it detect the abnormal calibration data
2023-12-30 fix a bug that the XY offset is not used
    [BDsensor.py]
2024-01-02 Fix pins init checking
    [BD_sensor.c]
2024-01-02 remove fixies from branch
    [BDsensor.py]
2024-01-02 optimize the homing process that maybe clash the bed
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2024-01-06 add reboot the bdsensor if detect the error data while homing.
    [BDsensor.py]
2024-01-17 sync the code from klipper that fixed the multi mcu timeout bug
    [BDsensor.py]
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2024-02-02 support BDsensor(v1.1b or v1.2b) works as switch sensor
    support BDsensor(v1.1b or v1.2b) works as switch sensor
    this can fix the bed cashing while homing.
    require the bdsensor 's firmware is v1.1b or v1.2b.
    [BD_sensor.c, BDsensor.py]
2024-02-05 add new firmware for BDsensor that support switch and strain gauge mode
2024-02-12 support collision homing that require the new firmware of V1.1b or V1.2b later version
    [BDsensor.py]
2024-02-13 fix a syntax error by the last commit
    [BDsensor.py]
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2024-02-16 clear the log code for the collision sensing
    [BDsensor.py]
2024-02-24 clear the code of collision homing
    [BDsensor.py]
2024-02-24 optimizate code of collision homing.
    [BDsensor.py]
2024-02-25 fix a bug for the nozzle collision homing
    [BDsensor.py]
2024-02-26 fix a compile error for none 32bit mcu
    [BD_sensor.c, BDsensor.py]
2024-02-27 sync code into beta version for the fixing a compile error
    [BD_sensor.c]
2024-02-28 rename the stl file
    [coil_case_withoutcoil.stl, coilcase_empty.stl]
2024-02-28 fix a compile warning in beta
    [BD_sensor.c]
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2024-03-03 add a new setting "collision_calibrate" for if BDsensor calibrate with collision.
    [BDsensor.py]
2024-03-13 Update BDsensor.py
    z_offset for collision homing
    [BDsensor.py]
2024-03-18 optimize the collision sensing
    [BD_sensor.c, BDsensor.py]
2024-03-21 collision adjust: z_offset for the collision
    [BDsensor.py]
2024-03-24 fix a bug on the 8 bit atmega mcu
    [BD_sensor.c, BDsensor.py]
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2025-01-30 fix error G28 called recursively while calibration
    [BDsensor.py]
2025-02-21 fix the z_offset bug by the latest update for auto calibration
    [BDsensor.py]
2025-03-12 it can work with endstop pin and the sensor will only scan
2025-03-27 add z adjust limitation to the real time level while the sensor is at the edge of the bed, need to flash firmware.
2025-06-10 optimize the collision force for some printer( no need to flash firmware)
    [BDsensor.py]
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2025-12-14 update the 3D file of coil case
    [coil_case.step, coil_case.stl, coil_case2025.step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]
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2026-04-29 add schematic
    add schematic
    [PCB_case.stl, coil_case2025.step, coil_case2025.stl]
2026-05-30 fix a bug for probe_accuracy
    [BDsensor.py]
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

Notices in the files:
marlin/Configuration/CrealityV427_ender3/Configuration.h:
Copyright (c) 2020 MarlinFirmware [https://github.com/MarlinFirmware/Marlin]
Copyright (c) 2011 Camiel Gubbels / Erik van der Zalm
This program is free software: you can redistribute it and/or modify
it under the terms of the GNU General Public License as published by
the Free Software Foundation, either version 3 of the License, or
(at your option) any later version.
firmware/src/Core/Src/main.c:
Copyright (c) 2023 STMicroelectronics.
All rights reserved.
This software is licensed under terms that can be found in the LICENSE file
